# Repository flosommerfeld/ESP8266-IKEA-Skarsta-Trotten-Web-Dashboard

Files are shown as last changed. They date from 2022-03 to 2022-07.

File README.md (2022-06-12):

<h1>
  <p align="center">
     ESP8266 IKEA Skarsta/Trotten Web Dashboard
  </p>
</h1> 

<p align="center">
ESP8266 project for adjusting the height of an <a href="https://www.ikea.com/de/de/p/trotten-schreibtisch-sitz-steh-weiss-s99429578/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">IKEA Skarsta/Trotten table</a> via a Web Dashboard.
</p>

<p align="center">
The table only comes with a crank from the factory - this project replaces the manual crank with a motor so there is no more need for manual cranking. This project aims to show you how to digitize an IKEA table.
</p>

<div align="center">
   
   
</div>

<p align="center">
  <a href="#showcase">Showcase</a> •
  <a href="#features">Features</a> •
  <a href="#circuit">Circuit</a> •
  <a href="#3d-model"> 3D Model</a> •
  <a href="#finite-state-machine">Finite State Machine</a> •
  <a href="#dependencies">Dependencies</a> •
  <a href="#hardware">Hardware</a> •
  <a href="#credits">Credits</a> •
  <a href="#license">License</a>
</p>

## Showcase

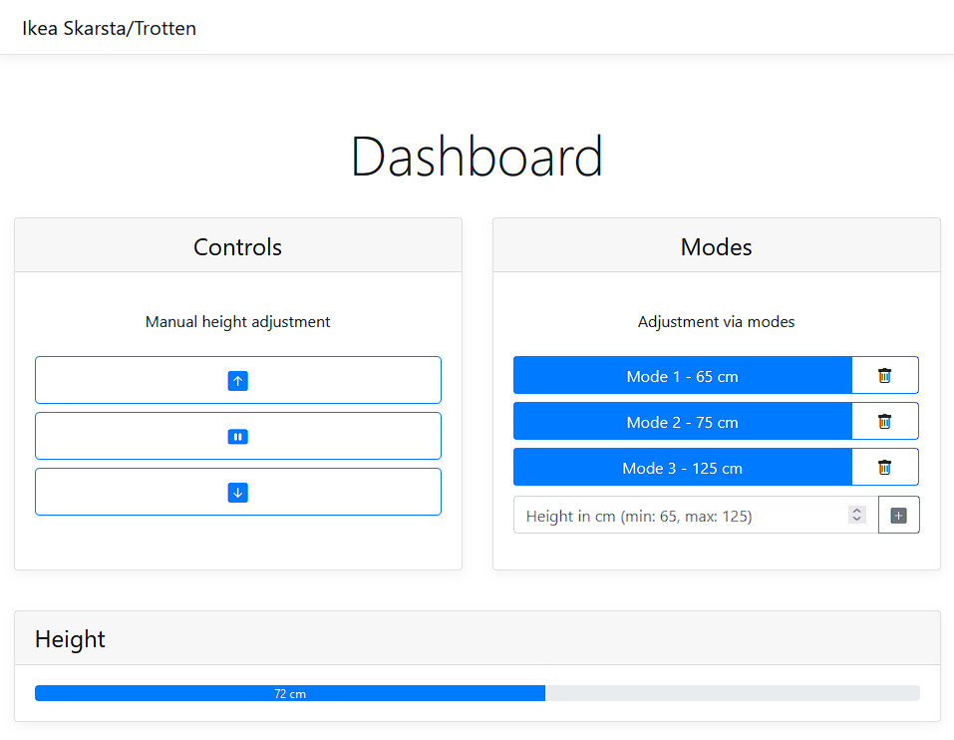
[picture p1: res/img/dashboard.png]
Dashboard


## Features

- Web Dashboard is accessible from anywhere within your WiFi network
- No more manual cranking the table up or down
- Controlling the height of the table via the web
- Setting custom height modes via the web
- Current height is being frequently displayed

## Circuit

This circuit ([source file](res/circuit.fzz)) was designed with [Fritzing](https://fritzing.org/). Please see the hardware section near the end of the README for a detailed list of the used hardware components which are shown in the circuit.
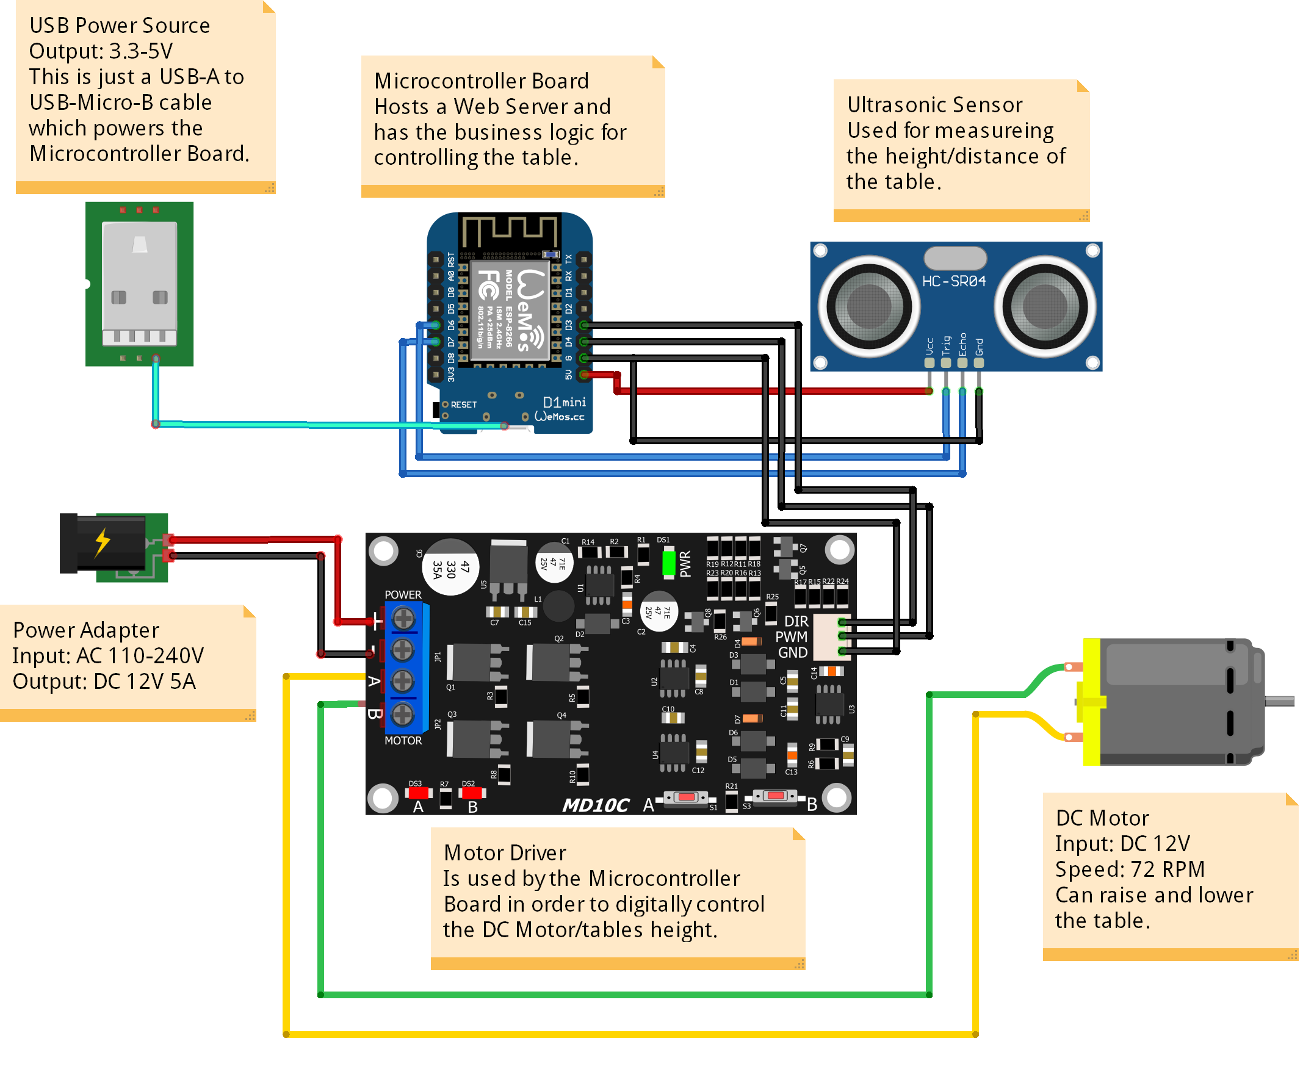
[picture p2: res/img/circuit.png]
Circuit


## 3D Model

The [3D models](#credits) of user pashiran were used and adapted in this project.
Small holes were drilled into the table in order to screw the `Body1.stl` with M3 screws to it. After installing `Body1.stl`, the  `Body3.stl` (case) was screwed on to it.  Some M3 insert nuts were installed to `Body1.stl` with a soldering iron.

Body1.stl ([Download](https://content.instructables.com/ORIG/FHK/3039/KJWV4CPV/FHK3039KJWV4CPV.stl)) | Body3.stl ([Download](https://content.instructables.com/ORIG/F6Q/4HMT/KJWV4CPX/F6Q4HMTKJWV4CPX.stl))
--- | ---
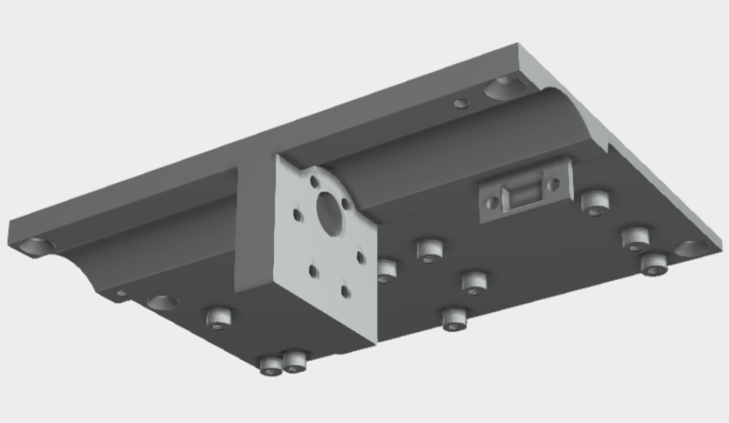
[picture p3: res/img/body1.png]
3D model 1
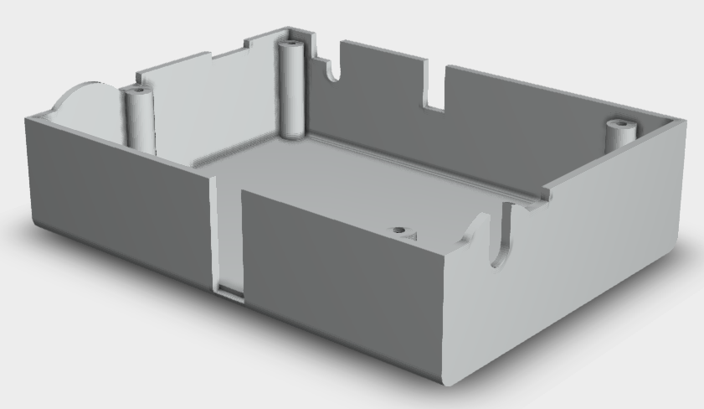
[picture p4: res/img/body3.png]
3D model 2
 | 

## Finite State Machine

The implementation is based on the following FSM:
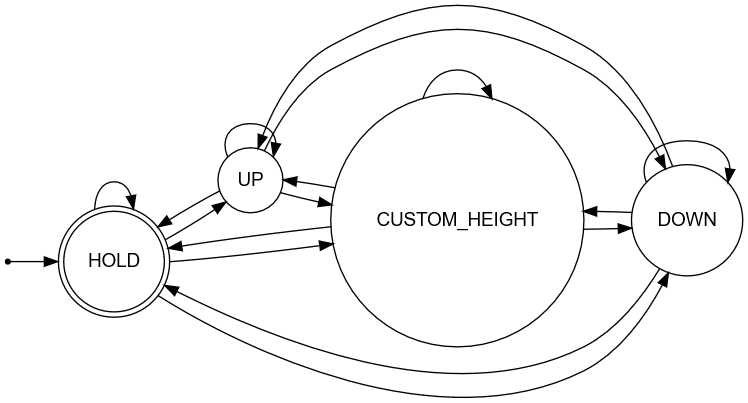
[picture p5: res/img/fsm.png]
FSM


State transitions to the current state i.e. `UP`->`UP` happen when the user requests nothing after requesting the table to go up. The implementation takes care of stopping if the user hasn't stopped the table manually before reaching the maximum height and vice versa. `CUSTOM_HEIGHT` automatically transitions to `HOLD` whenever the requested height has been reached.
All other state transitions are done when the user requests something via the Web Dashboard through the following routes:

- `/motor/<string: action>/` with `action` being `up`, `down`, `stop`
- `/height/<string: height_in_cm>/` with `height_in_cm` in the range from `60` to `160`.

## Dependencies

Used dependencies for this project are:

- [Arduino Library for Cytron Motor Drivers](https://github.com/CytronTechnologies/CytronMotorDriver), used to control the motor
- [HCSR04 ultrasonic sensor Library for Arduino](https://github.com/gamegine/HCSR04-ultrasonic-sensor-lib), used to read the distance from the ultrasonic sensor

The dependencies can be installed via the [standard procedure for installing Arduino libraries](https://docs.arduino.cc/software/ide-v1/tutorials/installing-libraries):

1. Open the Arduino IDE, select `Sketch` -> `Include Library` -> `Manage Libraries...`.
2. Search for `Cytron Motor Drivers Library by Cytron Technologies Sdn Bhd`/`HCSR04 ultrasonic sensor Library by gamegine`.
3. Click `Install` to install the library.
4. Restart the Arduino IDE.

## Hardware

The hardware selection and 3D models of this project are mainly based on the [Instructable](https://www.instructables.com/Motorizing-an-IKEA-SKARSTA-Table/) of user pashiran. In comparison, this project uses a website ("web dashboard") for controlling the table height and a ultrasonic sensor for measuring the height instead of an optical endstop. There are no hardware switches, just the website which can be accessed via the hosted ESP8266 server (which shall be in the same network as your clients).

- Development Board:
  - [WeMos D1 Mini Pro V 3,0 NodeMcu 4MB/16MB ESP8266 CH340G Nodemcu V2](https://de.aliexpress.com/item/32831353752.html?gatewayAdapt=glo2deu&spm=a2g0o.order_list.0.0.21ef5c5fNLvT1b)
- Motor:
  - [Bringsmart 37GB555 DC 12 V 72 RPM](https://de.aliexpress.com/item/32968002582.html?gatewayAdapt=glo2deu&s...)
- Motor Driver Board:
  - [Cytron MD10C 10Amp 5V-30V DC Motor Driver](https://www.cytron.io/p-10amp-5v-30v-dc-motor-driver)
- Power Adapter
  - [Arote LED Trafo with 5.5x2.1mm Female Terminal Block 2 pin, Output: 12V 5A, Input: AC110-240V, 60W:](https://www.amazon.de/Netzteil-Netzadapter-Transformator-Kaltger%C3%A4testecker-Streifen/dp/B07FNMKTBL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)
- Shaft Coupling (6x7mm):
  - [D19L25 6x7mm](https://de.aliexpress.com/item/32874492868.html?gatewayAdapt=glo2deu&spm=a2g0o.order_list.0.0.21ef5c5fNLvT1b)
- 6mm hex wrench (cut the bent part)
- Ultrasonic Sensor:
  - [HC-SR04 Ultrasonic Sensor](https://de.aliexpress.com/item/32713522570.html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)
- [3D Print](#credits)
- Table
  - [Ikea Skarsta/Trotten](https://www.ikea.com/nl/nl/p/skarsta-trotten-bureau-zit-sta-beige-wit-s29477959/)

Total costs approx. 48 € if you are patient enough to wait for the Aliexpress delivieries from China. The table and 3D printed model are not included in my calculation.

## Credits

- [3D design files](https://www.instructables.com/Motorizing-an-IKEA-SKARSTA-Table/) by user pashiran
- [Arduino library for HCSR04 ultrasonic sensor](https://github.com/gamegine/HCSR04-ultrasonic-sensor-lib) by gamegine
- [Arduino library for Cytron Motor Drivers](https://github.com/CytronTechnologies/CytronMotorDriver) by Cytron
- [Arduino ESP8266 Web Server library](https://github.com/esp8266/Arduino/tree/master/libraries/ESP8266WebServer) by Arduino
- [Bootstrap HTML, CSS, JS Framework](https://getbootstrap.com/) by Bootstrap

## License

The contents of this repository are covered under the [GPLv3 license](LICENSE).

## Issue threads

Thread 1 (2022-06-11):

Replace predefined modes with ones that can be customized

flosommerfeld, 2022-06-11:
At the moment the predefined modes 75 cm, 125 cm, 150 cm can't be changed. This shall be fixed in the client by saving the new modes in the local storage etc.

Closed 2022-06-12.

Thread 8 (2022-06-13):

Can't manually stop the motor if a mode is currently applied

flosommerfeld, 2022-06-13:
Also everything else is not possible. The whole web dashboard crashes if it is loaded in a new tab etc. While the height adjusment is running the pseudo-concurrency is not working.

Closed 2022-06-13.

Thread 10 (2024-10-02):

Mention explicitly that D1 mini should be with WiFi module

msch4ever, 2024-10-02:
Your link provided to AliExpres contains several boards and the first item is without wifi

msch4ever, 2024-10-02:
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

msch4ever, 2024-10-28:
Nah... my bad. Not an issue. Good link

Closed 2024-10-28.

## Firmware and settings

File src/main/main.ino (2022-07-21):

#include <ESP8266WiFi.h>
#include <WiFiClient.h>
#include <ESP8266WebServer.h>
#include <ESP8266mDNS.h>
#include <uri/UriBraces.h>
#include <uri/UriRegex.h>
#include "index.h"
#include <HCSR04.h>
#include "CytronMotorDriver.h"

#define DEBUG

/* WiFi configuration */
#ifndef STASSID
#define STASSID "SSID of the WLAN router" // PUT YOUR "WIFI NAME" HERE
#define STAPSK  "passphrase" // PUT YOUR WIFI PASSWORD HERE
#define OPT_HOSTNAME  "table" // Optional hostname
#endif
const char *SSID = STASSID;
const char *PASSWORD = STAPSK;
const char *HOSTNAME = OPT_HOSTNAME;

/* Pin configuration */
#define MOTOR_DRIVER_PWM D4 // pwm pin for the motor driver board
#define MOTOR_DRIVER_DIR D3 // direction pin for the motor driver board
#define MOTOR_SPEED 255 // speed of the motor from 0-250
#define ULTRASONIC_SENSOR_ECHO_PIN D7 // HC-SR04 ultrasonic sensor - Echo Pin 
#define ULTRASONIC_SENSOR_TRIGGER_PIN D6 // HC-SR04 ultrasonic sensor - Trigger Pin

/* Configure ESP8266 web server */
ESP8266WebServer server(80); // use port 80

/* Configure the motor driver */
CytronMD motor(PWM_DIR, MOTOR_DRIVER_PWM, MOTOR_DRIVER_DIR);

/* Configure ultrasonic sensor */
HCSR04 hc(ULTRASONIC_SENSOR_TRIGGER_PIN, ULTRASONIC_SENSOR_ECHO_PIN); // initialisation HCSR04 (ultrasonic sensor) (trig pin , echo pin)

/* States of the system */
typedef enum {
  UP, // table is supposed to go up
  DOWN, // table is supposed to go down
  HOLD, // table is supposed to do nothing -> hold still
  CUSTOM_HEIGHT // table goes up/down and holds as soon as it reached the custom height
} state_t;

/* Global state of the system. In HOLD by default -> motor will not move in this state */
state_t g_system_state = HOLD; //

/* Maximum and minimum height of the table in cm */
const unsigned int MOTOR_CASE_HEIGHT = 5; /* 5 cm */
const unsigned int TABLE_THICKNESS = 2; /* approx. 2 cm */
const unsigned int HEIGHT_DIFFERENCE = MOTOR_CASE_HEIGHT + TABLE_THICKNESS;
const unsigned int MAX_HEIGHT = 120;/* 120 cm is the offical maximum height from the IKEA manual */
const unsigned int MIN_HEIGHT = 70; /* 70 cm is the offical minimum height from the IKEA manual */

/* Height tolerance (in cm) which is needed because the ultrasonic sensor is not really accurate */
const unsigned int HEIGHT_TOLERANCE = 2; /* This used to be 5 cm but was reduced to 2 because of how slow the table motor is */

/* Global variable which shall hold the wanted custom height when requested */
int g_custom_height;


/* 
 * Displays the index/main page in the browser of the client
 */
void display_index() {
 String s = MAIN_page; // read HTML contents from the MAIN_page variable which was stored in the flash (program) memory instead of SRAM, see index.h
 server.send(200, "text/html", s); // send web page
}


/*
 * The server sends a redirection response to the client so it will go back to the homepage after requesting a state change,
 * e.g. when motor up was clicked it shall go back to the homepage
 */
void send_homepage_redirection() {
  server.sendHeader("Location","/"); // Client shall redirect to "/"
  server.send(303);
}


/*
 * Handles calls to the URI /motor/<string: action>/ and does state transitions:
 * if for example /motor/up is called, then the system will transition from the previous state
 * to the state UP. 
 */
void handle_motor_requests() {
  String action = server.pathArg(0); // retrieve the given argument/action

  if(action == "up"){
    g_system_state = UP;
  }
  else if(action == "stop"){
    g_system_state = HOLD;
  }
  else if(action == "down"){
    g_system_state = DOWN;
  }
  else {
    Serial.println("Error: Action is unknown"); // system will stay in its previous state
  }

  // send response
  send_homepage_redirection();
}


/*
 * Handles calls to the URI /height/<string: height_in_cm>/
 * If a height is given, then the system shall transition into the CUSTOM_HEIGHT state.
 */
void handle_height_requests() {
  int height = atoi((server.pathArg(0)).c_str()); // convert string parameter to integer

  // only change the state if the given height is in the height boundaries
  if(height >= MIN_HEIGHT and height <= MAX_HEIGHT) {
    g_custom_height = height; // set the custom height
    g_system_state = CUSTOM_HEIGHT; // transition to the custom height state
  }

  // send response
  send_homepage_redirection();
}


/*
 * Handles calls to the URI /height/
 * Responds with the current height of the ultrasonic sensor
 */
void handle_read_height_requests() {
  int height = get_current_height();
  server.send(200, "text/plain", String(height));
}


/**
 * Setup the output pins
 */
void setup_pins() {
  // Pin setup for motor controller
  pinMode(MOTOR_DRIVER_PWM, OUTPUT);
  pinMode(MOTOR_DRIVER_DIR, OUTPUT);
}


/**
 * Takes care of the wifi configuration
 */
void setup_wifi() {
  WiFi.mode(WIFI_STA);
  WiFi.hostname(OPT_HOSTNAME); // set HOSTNAME
  WiFi.begin(SSID, PASSWORD);

   // Wait for wifi connection
    while (WiFi.status() != WL_CONNECTED) {
      delay(500);
    Serial.print(".");
  }

  // Start the mDNS responder for esp8266.local
  if (MDNS.begin("esp8266")) {
    Serial.println("MDNS responder started");
  }
}


/**
 * Print information about the wifi connection:
 * SSID, IP, HOSTNAME
 */
void print_connection_info() {
  // Print connection info
  Serial.print("Connected to ");
  Serial.println(SSID);
  Serial.print("IP address: ");
  Serial.println(WiFi.localIP());
  Serial.print("HOSTNAME: ");
  Serial.println(WiFi.hostname().c_str());
}


/**
 * Register the routes of the server
 */
void register_server_routes() {
  server.on(F("/"), display_index); // route: /
  server.on(UriBraces("/motor/{}"), handle_motor_requests); // route: /motor/<string: action>/
  server.on(UriBraces("/height/{}"), handle_height_requests); // route: /height/<string: height_in_cm>/
  server.on(UriBraces("/height"), handle_read_height_requests); // route: /height/ - is being called from client javascript
}


/*
 * Login to the network, setup the server and register URI call handlers.
 */
void setup(void) {
  Serial.begin(115200);

  setup_wifi();

  #ifdef DEBUG
  print_connection_info();
  #endif

  register_server_routes();

  // Start the server
  server.begin();
  Serial.println("HTTP server started");
}


/*
 * Retrieves the current height of the table by getting the distance of the
 * ultrasonic sensor.
 */
int get_current_height() {
  delay(100); // > 60 ms measurement cycle to prevent trigger signal to the echo signal
  Serial.print("Current table height");
  Serial.println(hc.dist());
  return hc.dist() + HEIGHT_DIFFERENCE; // return height
}


/*
 * Raise the table until the max height is reached
 */
void raise_table() {
  if(MAX_HEIGHT >= get_current_height()) {
    motor.setSpeed(MOTOR_SPEED);
  }
  else {
    g_system_state = HOLD;  
  }
}


/*
 * Lower the table until the min height is reached
 */
void lower_table() {
  if(MIN_HEIGHT <= get_current_height()) {
    motor.setSpeed(-MOTOR_SPEED); // two's complement for negating the integer
  }
  else {
    g_system_state = HOLD;  
  }
}


/*
 * Stop the table at the current height
 */
void stop_table() {
   motor.setSpeed(0);
}


/*
 * Controls the motor based on the system state g_system_state. This is pretty much the core FSM implementation for the state transistions.
 */
void handle_output() {
  switch (g_system_state) {
        case UP:
            raise_table(); // motor go up
            break;
        case DOWN:
            lower_table(); // motor go down
            break;
        case HOLD:
            stop_table(); // stop the motor
            break;
        case CUSTOM_HEIGHT:
          // adjust the table height until the height tolerance is ok, e.g.: abs(150-130) = 20, abs(150-170) = 20
          if(abs(g_custom_height - get_current_height()) >= HEIGHT_TOLERANCE) {
            // check if the table is too high or too low and adjust
            if(g_custom_height < get_current_height()) {
              lower_table(); // lower the table
            }
            else{
              raise_table(); // raise the table
            }
            
          }
          else {
            // adjustment is finished, transistion to the hold state to stop the motor
            g_system_state = HOLD;
          }

          break;
        default:
            // stop the motor by transitioning to the hold state
            g_system_state = HOLD;
    }
}


/*
 * Main loop. Gets the current height, retrieves inputs and do state 
 * transitions and finally control the motor based on the state.
 */
void loop(void) {
  server.handleClient(); // gets input from a client
  handle_output(); // controls the height of the table based on the input
}

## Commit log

2021-06-22 Add arduino sketch
2022-03-18 add height boundaries to the motor control
2022-03-19 add use of cytron motor driver lib
2022-03-19 add first circuit
    [circuit.fzz]
2022-04-22 Add power adapter to README
2022-04-22 Add finished circuit
    [circuit.fzz]
2022-06-11 add folder for arduino sketch and remove old stuff
2022-06-11 Apply snake case to function names
2022-06-11 Apply upper case to macro names and other constants
2022-06-12 feat: replace predefined modes with ones that can be customized (#2)
    * Add logic for loading, saving and displaying modes
    * Fix bug
    * Add deleting and adding modes
    * Add ESP lib to credits
    * Update maximum table height
    [main.ino]
2022-06-12 feat: displaying the height in the dashboard (#4)
    * Add retrieving and displaying the table height in the dashboard
    * Add responding to height sensors read requests
    * Fix typo in MIME type
    * Fix redefenition
    * Fix ESP class has no member 'HOSTNAME'
    * Move images to seperate folder and update README
    * Update project description
    [main.ino]
2022-06-13 fix: remove pseudo-concurrency blocker (#9)
    * Fix bug by removing the while statement
    * Format code
    [main.ino]
2022-07-21 fix: minimum height of the table was too low
    [main.ino]
